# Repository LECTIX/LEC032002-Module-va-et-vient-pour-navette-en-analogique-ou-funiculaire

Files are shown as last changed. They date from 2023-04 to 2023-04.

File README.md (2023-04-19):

# LEC032002 - Module va et vient pour navette en analogique ou funiculaire
Fichiers sources pour le produit LEC032002

## Description du produit

- **AUTOMATIQUE** gérez votre train en mode navette ou votre funiculaire automatiquement
- **ACCÉLÉRATION** et freinage progressifs
- **TEMPORISATION** réglable entre 1 s et plus de 3 min
- **SIMPLICITÉ** Réglage facile de la vitesse maximum, du temps d'arrêt, de la courbe d'accélération et de freinage
- **SÉCURITÉ** Protection contre les courts circuits

## Utiliser les fichiers sources pour fabriquer le produit

Il n'est **pas nécessaire de savoir souder ou d'être bon en électronique** pour se procurer ce produit. Grâce aux fichiers sources publiés ici, vous pouvez être en mesure de faire fabriquer ce produit par un sous traitant.

**ATTENTION** ce produit nécessite une programmation afin de pouvoir fonctionner. Vous devez pour cela posséder le programmateur et programmer vous même la carte. Cette étape peut nécessiter des connaissances techniques, si nécessaire, nous vous encourrageons à vous rapprocher d'un club.

### Faire fabriquer chez un sous traitant

Il est aujourd'hui possible de faire fabriquer à moindre cout des cartes électroniques. Nous recommendons [JLCPCB](https://jlcpcb.com/) si vous voulez aller au moins cher. Si vous préférez un acteur européen, [eurocircuits](https://www.eurocircuits.com/) est un des acteurs reconnus.

IMAGE ALT TEXT (http://www.youtube.com/watch?v=RXGGvsUtz0c "TUTO : faire fabriquer un produit LECTIX")

1. Télécherger les sources de ce produit en cliquant sur le bouton `Code`, puis `Download ZIP`.
1. Décompresser le dossier.
1. Les fichiers pour la fabrication se trouvent dans le répertoire `hardware/prod`.
1. Se connecter sur [https://cart.jlcpcb.com/quote](https://cart.jlcpcb.com/quote)
1. Cliquer sur le bouton `Add gerber file` et sélectionner le fichier `gerbers.zip`.
1. Sélectionnez la quantité de cartes que vous souhaitez dans le champs `PCB Qty`.
1. Laisser toutes les autres options par défaut, puis cliquez sur le toggle switch en face de `PCB Assembly`, et enfin sur le bouton `confirm`.
1. Une preview de la carte électronique sans les composants doit apparaitre. Cliquez sur `NEXT`.
1. Cliquez sur le bouton `Add BOM File`, puis sélectionnez le fichier `bom.csv`
1. Cliquez sur le bouton `Add CPL File`, puis sélectionnez le fichier `pos.csv`
1. **Vérifier que tous les composants sont en stock** et bien sélectionnés, puis cliquez sur `NEXT`.
1. Une preview de la carte avec ses composants apparait. Continuer le chemin en cliquant sur `NEXT`.
1. Le prix final apparait. Sélectionnez la catégorie du produit, puis cliquez sur `SAVE TO CART`.
1. Une fois sauvegardé dans votre panier, vous pouvez valider votre commande et choisir le moyen d'acheminement. Afin de ne pas avoir à se préoccuper des frais de douane, nous vous conseillons de choisir une méthode d'expédition DDP.

Vous receverez vos cartes sous 1 à 3 semaines. 

**Nous ne sommes en aucun cas responsables des cartes qui arriveraient défectueuses ou non fonctionnelles.**

### Modifications des fichiers sources

Installez kicad 6 (ou version supérieure), et ouvrez le fichier LEC032002.kicad_pro

### Programation

Pour programmer le module, vous devez posséder
- un programmateur AVR type USBASP
- une sonde Tag-Connect TC2050

Le firmware se trouve dans le dossier du même nom. Il est recommandé d'utiliser VS-code et platform-io pour programmer la carte. Pour ce faire, branchez le programmateur à votre PC et à la carte à programmer, puis rentrer les commandes suivantes :

```
cd firmware
platformio run --target fuses && platformio run --target upload
```

### Regénérer les fichiers gerber, BOM, et position (Optionnel)

Peut se faire simplement en utilisant kikit :

```
cd hardware
docker run --rm -w /kikit -v $PWD:/kikit yaqwsx/kikit kikit fab jlcpcb --assembly --no-drc --schematic LEC032002.kicad_sch --field LCSC --corrections JLCPCB_CORRECTION --nametemplate LEC032002_{} LEC032002.kicad_pcb prod/

```
## Notices
[Manuel FR](docs/manual_fr.pdf)

## License
Tous nos fichiers sont plubliés sous les licenses
- CERN Open Hardware Licence Version 2 - Strongly Reciprocal pour ce qui touche au hardware
- GNU General Public License v3.0 pour tout ce qui est software

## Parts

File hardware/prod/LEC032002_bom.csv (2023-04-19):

Comment | Designator | Footprint | LCSC
100nF | C1,C3,C5,C7,C8,C9 | Capacitor_SMD:C_0603_1608Metric | C14663
100uF | C2,C6 | Capacitor_SMD:CP_Elec_6.3x7.7 | C249982
MB10S | D1 | Package_TO_SOT_SMD:TO-269AA | C2488
LED_green | D2 | LED_SMD:LED_0603_1608Metric | C72043
M7 | D3,D4,D5,D6,D7,D8,D9,D10 | Diode_SMD:D_SMA | C95872
LED_red | D11 | LED_SMD:LED_0603_1608Metric | C2286
Screw_Terminal_01x02_green | J1 | 0_connectors:TerminalBlock_bornier-2_P5.08mm-green | C395849
Screw_Terminal_01x02_blue | J2,J3,J4,J5 | 0_connectors:TerminalBlock_bornier-2_P5.08mm-blue | C430621
10k | R1,R2,R3,R9 | Resistor_SMD:R_0603_1608Metric | C25804
27R | R4,R5 | Resistor_SMD:R_0603_1608Metric | C25190
100k | R6,R7 | Resistor_SMD:R_0603_1608Metric | C25803
pot_smd_100k_3362P | RV1,RV2,RV3,RV4 | 0_potentiometers:BOURNS-3362P_pot | C118966
ATtiny24A-SSU | U1 | Package_SO:SOIC-14_3.9x8.7mm_P1.27mm | C14909
78L05G-AB3-R | U2 | Package_TO_SOT_SMD:SOT-89-3 | C71136
MP6515 | U3 | Package_SO:HTSSOP-16-1EP_4.4x5mm_P0.65mm_EP3.4x5mm_Mask3x3mm_ThermalVias | C114139
LTV-814S-TA1 | U4,U5 | Package_DIP:SMDIP-4_W9.53mm_Clearance8mm | C125118

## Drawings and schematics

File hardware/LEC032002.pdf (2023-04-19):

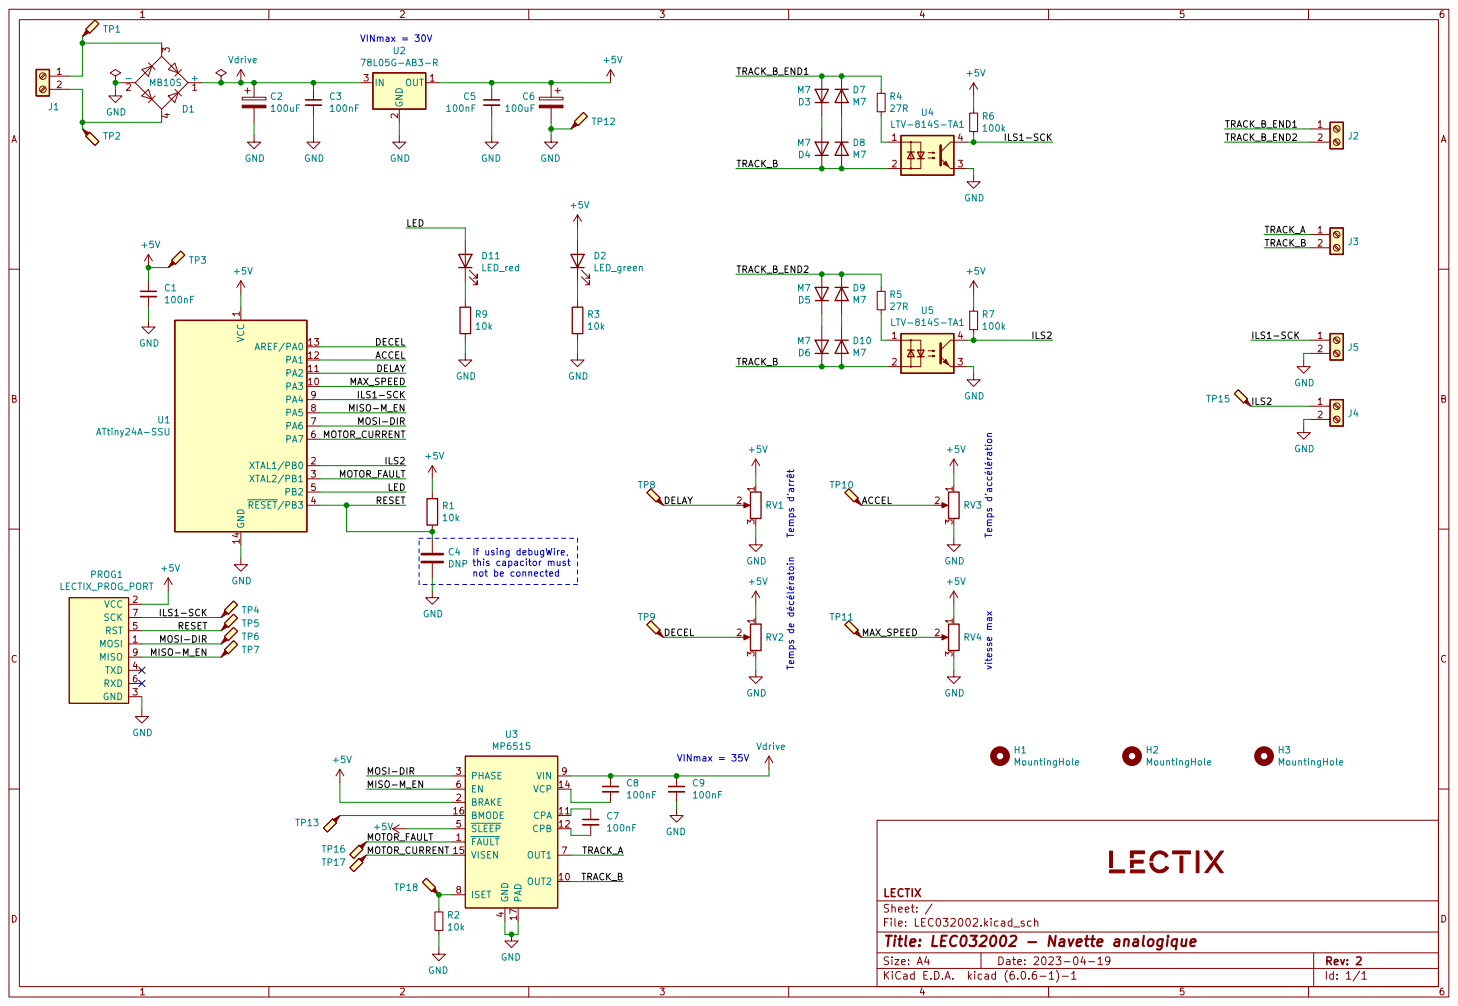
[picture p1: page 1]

1 PA3 10 PA2 11 PA1 12 AREF/PA0 13 GND 14 XTAL1/PB0 2 XTAL2/PB1 3 ~{RESET}/PB3 4 PB2 5 PA7 6 PA6 7 PA5 8 PA4 9 U1 ATtiny24A-SSU GND MOSI 1 VCC 2 GND 3 TXD 4 RST 5 RXD 6 SCK 7 MISO 9 PROG1

TRACK_A MISO-M_EN MOSI-DIR MISO-M_EN

Id: 1/1 Title: LEC032002 - Navette analogique

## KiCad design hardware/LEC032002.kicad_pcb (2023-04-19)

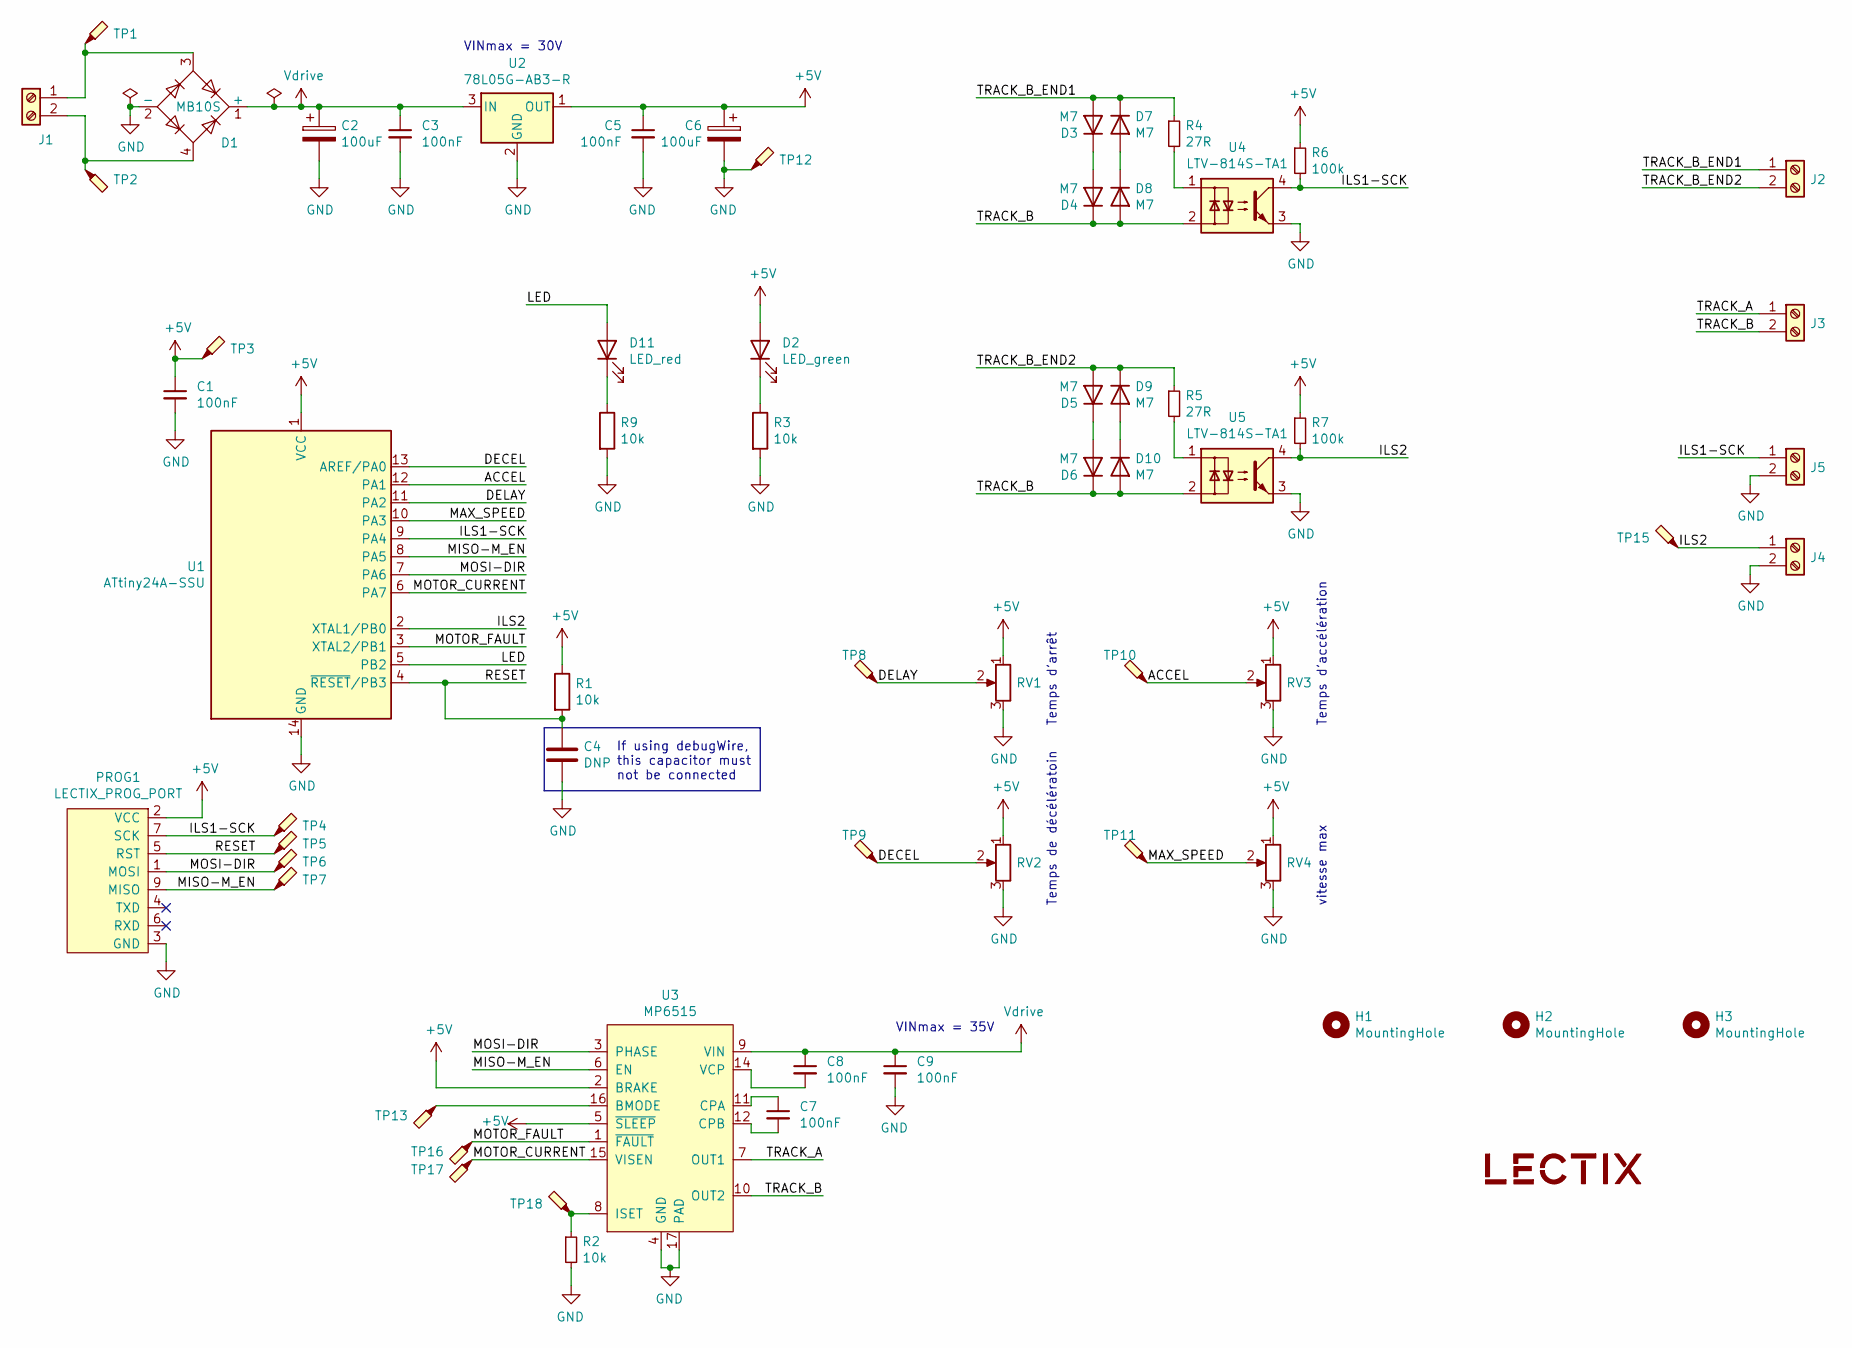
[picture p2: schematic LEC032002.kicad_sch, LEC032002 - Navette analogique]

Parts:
C1, C3, C5, C7, C8, C9: 100nF; C_0603_1608Metric; LCSC C14663
C2, C6: 100uF; CP_Elec_6.3x7.7; LCSC C249982
C4: DNP; C_0603_1608Metric; LCSC DNP
D1: MB10S; TO-269AA; LCSC C2488
D2: LED_green; LED_0603_1608Metric; MPN 19-217/GHC-YR1S2/3T; LCSC C72043
D3, D4, D5, D6, D7, D8, D9, D10: M7; D_SMA; MPN M7; LCSC C95872
D11: LED_red; LED_0603_1608Metric; LCSC C2286
H1, H2, H3: MountingHole; MountingHole_3.2mm_M3; LCSC DNP
J1: Screw_Terminal_01x02_green; TerminalBlock_bornier-2_P5.08mm-green; MPN DB126V-5.0-2P-GN; LCSC C395849
J2, J3, J4, J5: Screw_Terminal_01x02_blue; TerminalBlock_bornier-2_P5.08mm-blue; MPN DB301V-5.0-2P-BU-P; LCSC C430621
LOGO1: logo_lectix_25mm; Logo_10mm; LCSC DNP
PROG1: LECTIX_PROG_PORT; Tag-Connect_TC2050-IDC-FP_2x05_P1.27mm_Vertical; LCSC DNP
R1, R2, R3, R9: 10k; R_0603_1608Metric; LCSC C25804
R4, R5: 27R; R_0603_1608Metric; LCSC C25190
R6, R7: 100k; R_0603_1608Metric; LCSC C25803
RV1, RV2, RV3, RV4: pot_smd_100k_3362P; BOURNS-3362P_pot; MPN 3362P-1-104; LCSC C118966
TP1, TP2, TP3, TP4, TP5, TP6, TP7, TP8, TP9, TP10, TP11, TP12, TP13, TP15, TP16, TP17, TP18: TestPoint_Probe; TestPoint_Pad_D1.0mm; LCSC DNP
U1: ATtiny24A-SSU; SOIC-14_3.9x8.7mm_P1.27mm; LCSC C14909
U2: 78L05G-AB3-R; SOT-89-3; MPN 78L05G-AB3-R; LCSC C71136
U3: MP6515; HTSSOP-16-1EP_4.4x5mm_P0.65mm_EP3.4x5mm_Mask3x3mm_ThermalVi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; MPN MP6515GF-Z; LCSC C114139
U4, U5: LTV-814S-TA1; SMDIP-4_W9.53mm_Clearance8mm; MPN LTV-814S-TA1; LCSC C125118

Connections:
+5V: C1.1, C5.1, C6.1, D2.2 (A), PROG1.2 (VCC), R1.1, R6.1, R7.1, RV1.1, RV2.1, RV3.1, RV4.1, TP3.1, U1.1 (VCC), U2.1 (OUT), U3.2 (BRAKE), U3.5 (~SLEEP)
/ACCEL: RV3.2, TP10.1, U1.12 (PA1)
/DECEL: RV2.2, TP9.1, U1.13 (AREF/PA0)
/DELAY: RV1.2, TP8.1, U1.11 (PA2)
/ILS1-SCK: J5.1, PROG1.7 (SCK), R6.2, TP4.1, U1.9 (PA4), U4.4
/ILS2: J4.1, R7.2, TP15.1, U1.2 (XTAL1/PB0), U5.4
/LED: D11.2 (A), U1.5 (PB2)
/MAX_SPEED: RV4.2, TP11.1, U1.10 (PA3)
/MISO-M_EN: PROG1.9 (MISO), TP7.1, U1.8 (PA5), U3.6 (EN)
/MOSI-DIR: PROG1.1 (MOSI), TP6.1, U1.7 (PA6), U3.3 (PHASE)
/MOTOR_CURRENT: TP17.1, U1.6 (PA7), U3.15 (VISEN)
/MOTOR_FAULT: TP16.1, U1.3 (XTAL2/PB1), U3.1 (~FAULT)
/RESET: C4.1, PROG1.5 (RST), R1.2, TP5.1, U1.4 (~RESET/PB3)
/TRACK_A: J3.1, U3.7 (OUT1)
/TRACK_B: D4.1 (K), D6.1 (K), D8.2 (A), D10.2 (A), J3.2, U3.10 (OUT2), U4.2, U5.2
/TRACK_B_END1: D3.2 (A), D7.1 (K), J2.1, R4.1
/TRACK_B_END2: D5.2 (A), D9.1 (K), J2.2, R5.1
GND: C1.2, C2.2, C3.2, C4.2, C5.2, C6.2, C9.2, D1.2 (-), J4.2, J5.2, PROG1.3 (GND), PROG1.8 (GND), PROG1.10 (GND), R2.2, R3.2, R9.2, RV1.3, RV2.3, RV3.3, RV4.3, TP12.1, U1.14 (GND), U2.2 (GND), U3.4 (GND), U3.13 (GND), U3.17 (PAD), U4.3, U5.3
unnamed: C7.1, U3.11 (CPA)
unnamed: C7.2, U3.12 (CPB)
unnamed: C8.2, U3.14 (VCP)
unnamed: D1.3, J1.1, TP1.1
unnamed: D1.4, J1.2, TP2.1
unnamed: D2.1 (K), R3.1
unnamed: D3.1 (K), D4.2 (A)
unnamed: D5.1 (K), D6.2 (A)
unnamed: D7.2 (A), D8.1 (K)
unnamed: D9.2 (A), D10.1 (K)
unnamed: D11.1 (K), R9.1
unnamed: R2.1, TP18.1, U3.8 (ISET)
unnamed: R4.2, U4.1
unnamed: R5.2, U5.1
unnamed: TP13.1, U3.16 (BMODE)
Vdrive: C2.1, C3.1, C8.1, C9.1, D1.1 (+), U2.3 (IN), U3.9 (VIN)

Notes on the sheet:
VINmax = 35V
vitesse max
VINmax = 30V
Temps d’arrêt
If using debugWire, this capacitor must not be connected
Temps d’accélération
Temps de décélératoin

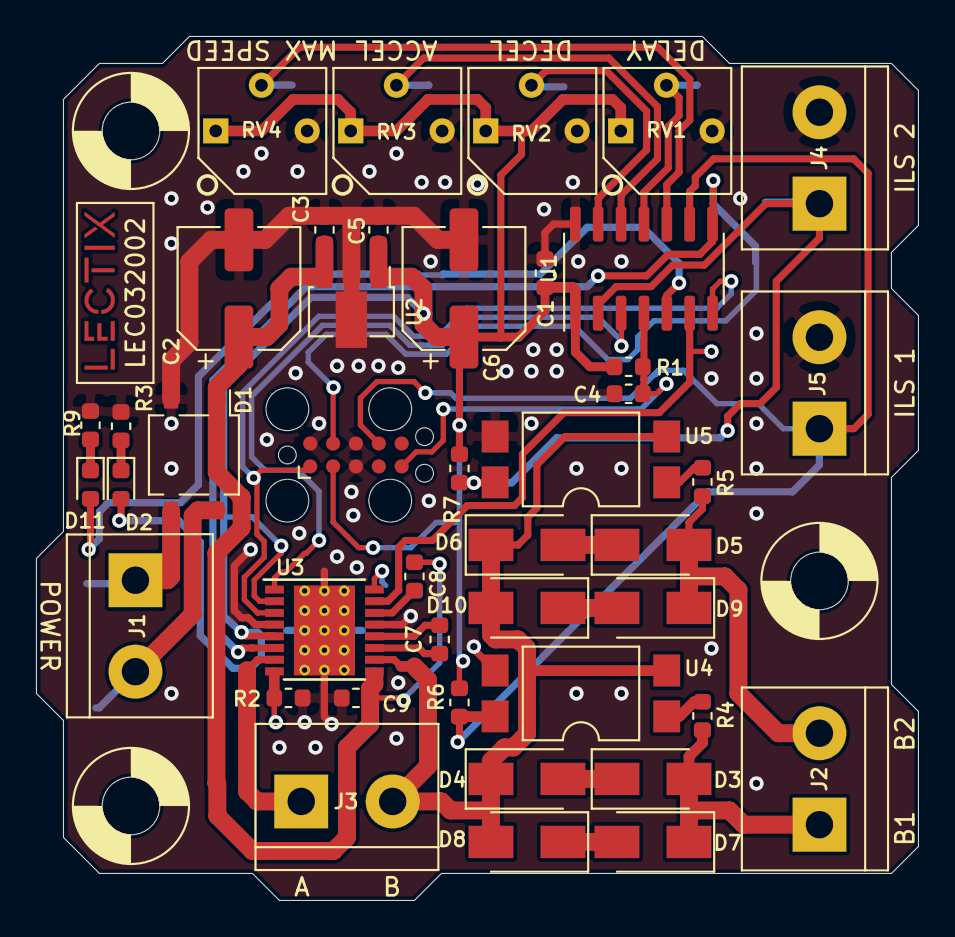
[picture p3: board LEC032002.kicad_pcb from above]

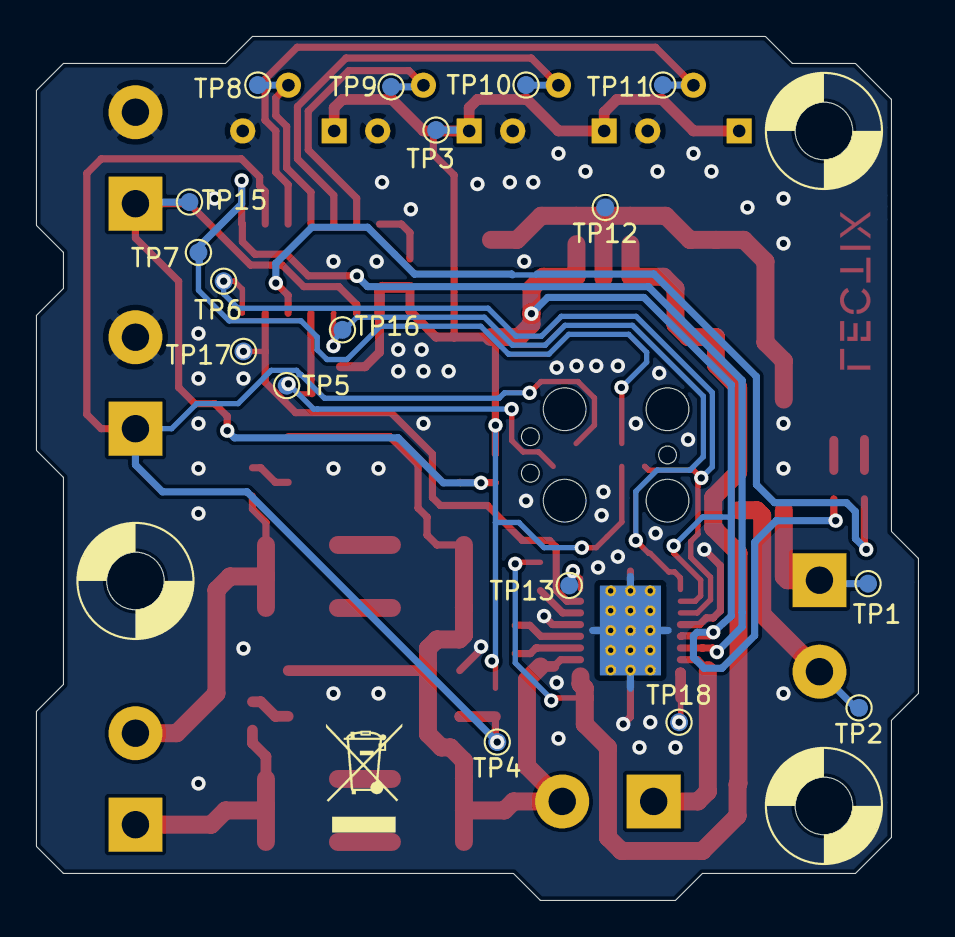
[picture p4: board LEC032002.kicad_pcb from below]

Board: 2 copper layers, 49.0 x 48.0 mm, 64 parts (17 on the bottom side), 34 nets.

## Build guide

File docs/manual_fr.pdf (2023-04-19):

# Module va et vient analogique

### LEC032002

☞ Avertissement : ce module n’est pas compatible avec les locomotives possédant un décodeur DCC (digital)!

## 1 Caractéristiques

- Mode navee (va et vient) automatique

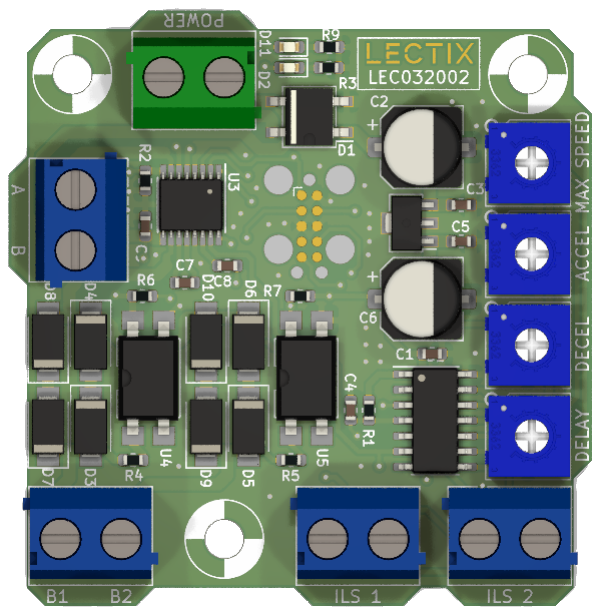
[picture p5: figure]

- Freinage et accélération progressive
- Détection des extrémités par analyse de la consommation de courant ou par capteurs ILS, pédales, ...
- Temporisation réglable entre 1 s et plus de 3 min
- Alimentation : 8 - 16 V DC
- Réglage facile de la vitesse maximum, du temps d’arrêt, de la courbe d’accélération et de freinage.
- Protection contre les courts circuits.
- 3 trous de fixation pour un montage facile.

## 2 Applications

- Mode navee (va et vient) automatique
- Mode navee (va et vient) via des capteurs de type ILS, pédale, ou équivalent
- Contrôle d’un funiculaire, ou de tout autre système motorisé DC

## 3 Specifications technique

Specification | Valeur | Unité
Temporisation avant redémarrage | 1 - 200 | sec
Tension d’alimentation | 8 - 16 | V DC
Intensité d’alimentation minimum recommandé | 1 | A
Intensité maximum en sortie du module | 1 | A

Table 1: Spécifications

LEC032002 - Module va et vient analogique rev 1.0.2 | 1

## 4 Utilisation

Le module va et vient analogique LEC032002 permet de créer facilement un mode navee automatisé pour votre réseau analogique. Il est également conçu pour piloter tout système à moteur DC devant changer de sens à intervalle régulier. On note notamment parmi ces systèmes le pilotage d’un funiculaire à l’aide d’un moteur et de 2 ILS.

L’installation du module est facile, le réglage des paramètres (vitesse maximum, temporisation avant redémarrage, accélération, freinage) se fait simplement en tournant les potentiomètres à l’aide d’un tournevis.

### 4.1 Installation et câblage du module pour un va et vient automatique

Le module doit être câblé tel que sur la figure 3.

1. Connecter une alimentation entre 8 et 16 V DC au bornier d’alimentation. Cee alimentation sera indirectement reliée à la voie, il faut donc que la tension d’alimentation soit compatible avec la tension d’utilisation de vos trains.
2. Connecter la voie sur le bornier de sortie (bornier "A B").
3. Connecter au choix :
- [Détection par consommation de courant] les rails droits isolés sur les 2 zones d’arrêt aux borniers B1 et B2 (Cf. Figure 1).
- [Détection par ILS, pédale, ...] les 2 ILS marquant le début des zones d’arrêt sur les borniers ILS1 et ILS2 (Cf. Figure 2).

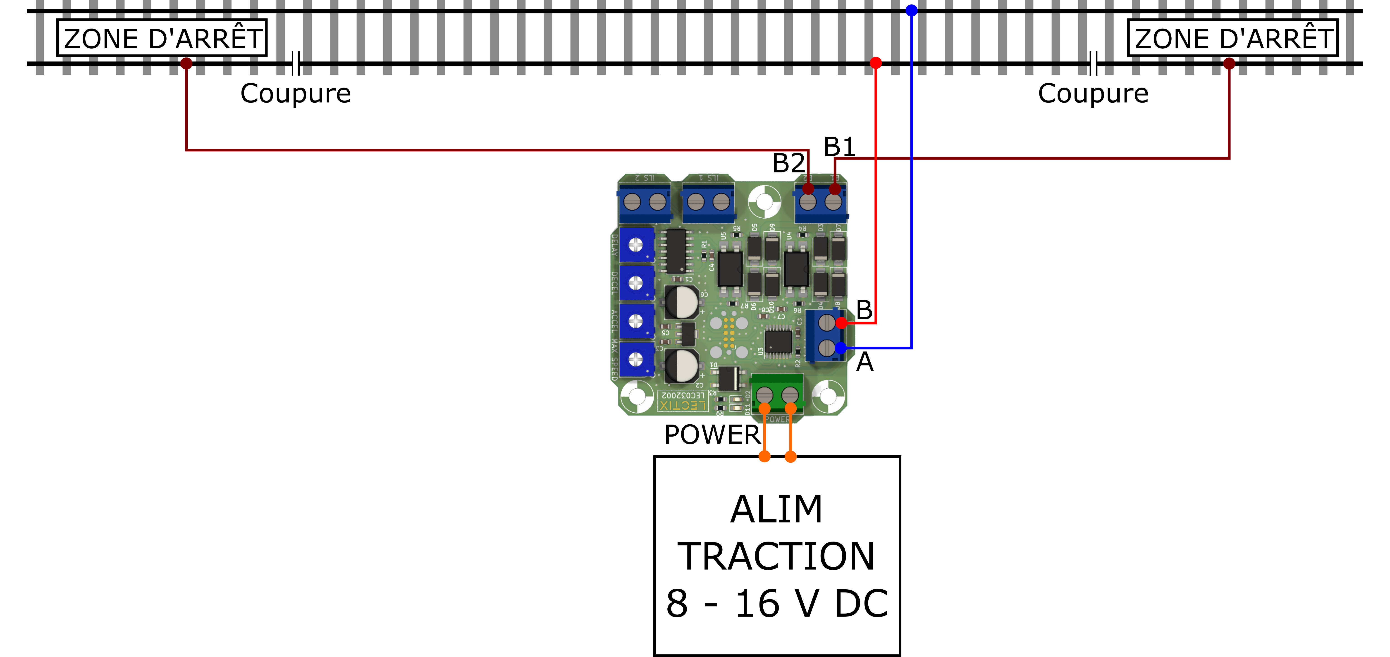
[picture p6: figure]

Figure 1: Schéma de câblage du module pour un va et vient analogique avec détection des zones de freinages par analyse de la consommation de courant.

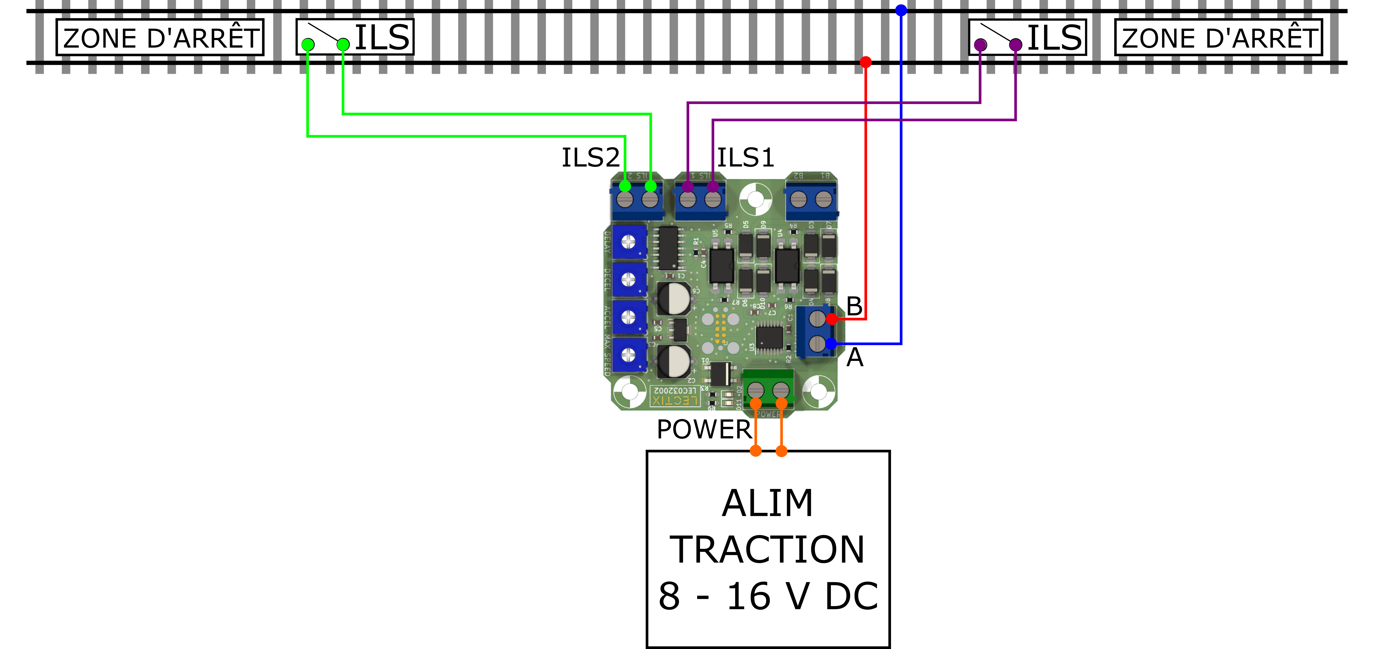
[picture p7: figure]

Figure 2: Schéma de câblage du module pour un va et vient analogique avec détection des zones de freinage par ILS (ou capteurs équivalents).

Une fois le module installé, il faut s’assurer que

- les ILS, capteurs de consommation (ou capteurs équivalents) soient bien branchés par rapport au sens de fonctionnement du train.
- le temps de freinage ne soit pas trop important, pour ne pas provoquer de collisions.

Pour ce faire, suivez les étapes suivantes :

1. mere le train au milieu de la voie (en dehors des zones de freinage donc)
2. tournez le potentiomètre du temps de décélération (DECEL) à fond dans le sens des aiguilles d’une montre. Cela aura pour eet d’arrêter immédiatement le train lorsqu’il rentrera dans la zone d’arrêt.
3. allumez le module en branchant son alimentation.

Si les capteurs sont branchés sur les bons borniers, le train doit s’arrêter immédiatement dès lors qu’il rentre dans la zone d’arrêt. Si le train continue au delà du capteur utilisé pour marquer le début de la zone de freinage, arrêtez immédiatement le module et inversez le branchement des capteurs (branchez les fils auparavant sur le bornier "ILS1" sur le bornier "ILS2", et inversement, ou respectivement "B1" et "B2" si utilisation des capteurs de consommation de courant).

Recommencez l’opération pour s’assurer que le fonctionnement est à présent correct, puis Rendez vous section suivante pour ainer le réglage du module.

### 4.2 Installation et câblage du module pour animer un funiculaire

1. Connecter une alimentation entre 8 et 16 V DC au bornier d’alimentation. Cee alimentation sera indirectement reliée à la voie, il faut donc que la tension d’alimentation soit compatible avec la tension d’utilisation du moteur.
2. Connecter le moteur sur le bornier de sortie (bornier "A B").
3. Connecter les 2 ILS sur les borniers ILS1 et ILS2.

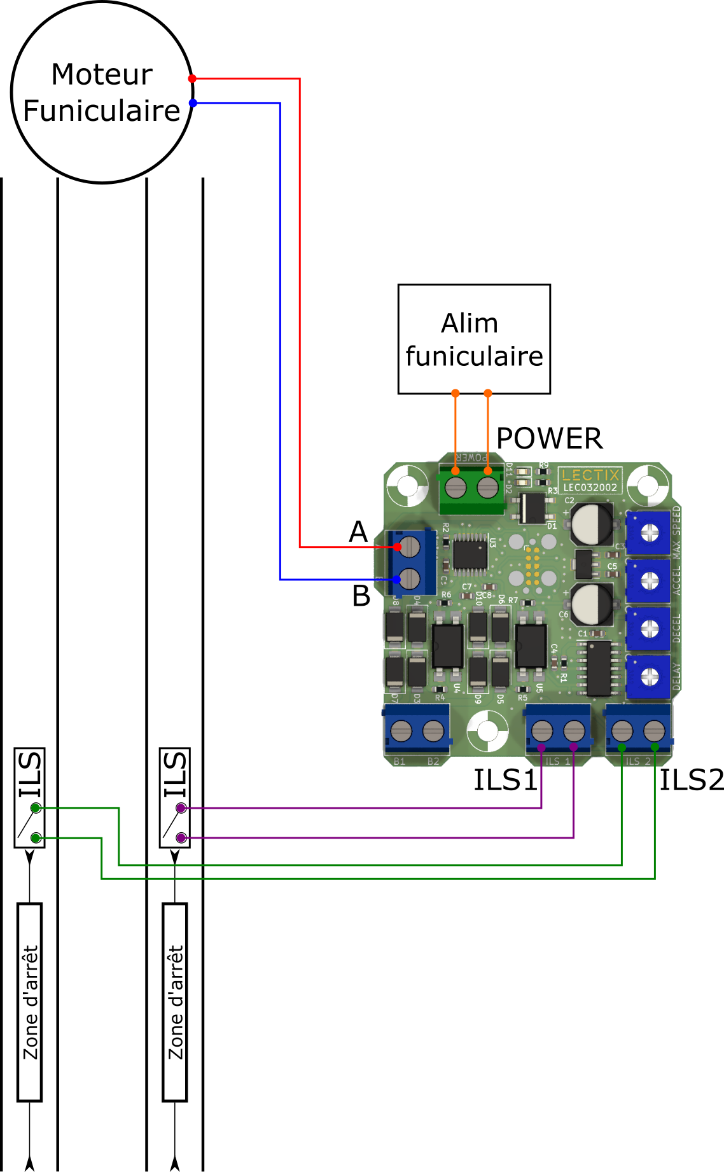
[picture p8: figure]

Figure 3: Schéma de câblage du module pour piloter un funiculaire.

Une fois le module installé, il faut s’assurer que

- les ILS (ou capteurs équivalents) soient bien branchés par rapport au sens de fonctionnement du moteur.
- le temps de freinage ne soit pas trop important, pour ne pas provoquer de collisions.

Pour ce faire, suivez les étapes suivantes :

1. mere le funiculaire au milieu des voies (en dehors des zones de freinage donc)
2. tournez le potentiomètre du temps de décélération (DECEL) à fond dans le sens des aiguilles d’une montre. Cela aura pour eet d’arrêter immédiatement le funiculaire lorsqu’il rentrera dans la zone d’arrêt.
3. allumez le module en branchant son alimentation.

Si les ILS sont branchés sur les bons borniers, le funiculaire doit s’arrêter immédiatement dès lors qu’il rentre dans la zone d’arrêt. Si le funiculaire continue au delà du capteur utilisé pour marquer le début de la zone de freinage, arrêtez immédiatement le module et inversez les 2 ILS (branchez les fils auparavant sur le bornier "ILS1" sur le bornier "ILS2", et inversement).

Recommencez l’opération pour s’assurer que le fonctionnement est à présent correct.

### 4.3 Réglage des paramètres

Cee section décrit une méthode pour régler les paramètres du module, à savoir vitesse maximum, temporisation avant redémarrage, temps d’accélération et de décélération. Il est conseillé d’utiliser un petit tournevis plat pour régler les potentiomètres.

☞ Note : Aention à ne pas forcer si le potentiomètre bloque, sous risque de détéri-

oration.

1. Pour commencer, régler tous les paramètres de la façon suivante :
- vitesse max ("MAX SPEED") => tourner le potentiomètre à fond dans le sens des aiguilles d’une montre.
- temporisation avant redémarrage ("DELAY") => tourner le potentiomètre à fond dans le sens inverse des aiguilles d’une montre.
- temps d’accélération ("ACCEL") => tourner le potentiomètre à fond dans le sens des aiguilles d’une montre.
- temps de décélération ("DECEL") => tourner le potentiomètre à fond dans le sens des aiguilles d’une montre.
2. Mere en route le module, et s’assurer que le va et vient fonctionne.
3. Régler la vitesse maximale qui vous convient le mieux en tournant, si nécessaire, le potentiomètre "MAX SPEED".
4. Régler le temps de décélération en tournant le potentiomètre ’DECEL’.
5. Régler le temps d’accélération en tournant le potentiomètre ’ACCEL’.
6. Enfin, régler la temporisation avant redémarrage en ajustant le potentiomètre "DELAY".

## 5 Dimensions

Le module dispose de 3 trous de fixation permeant de faire passer des vis de 3 mm.

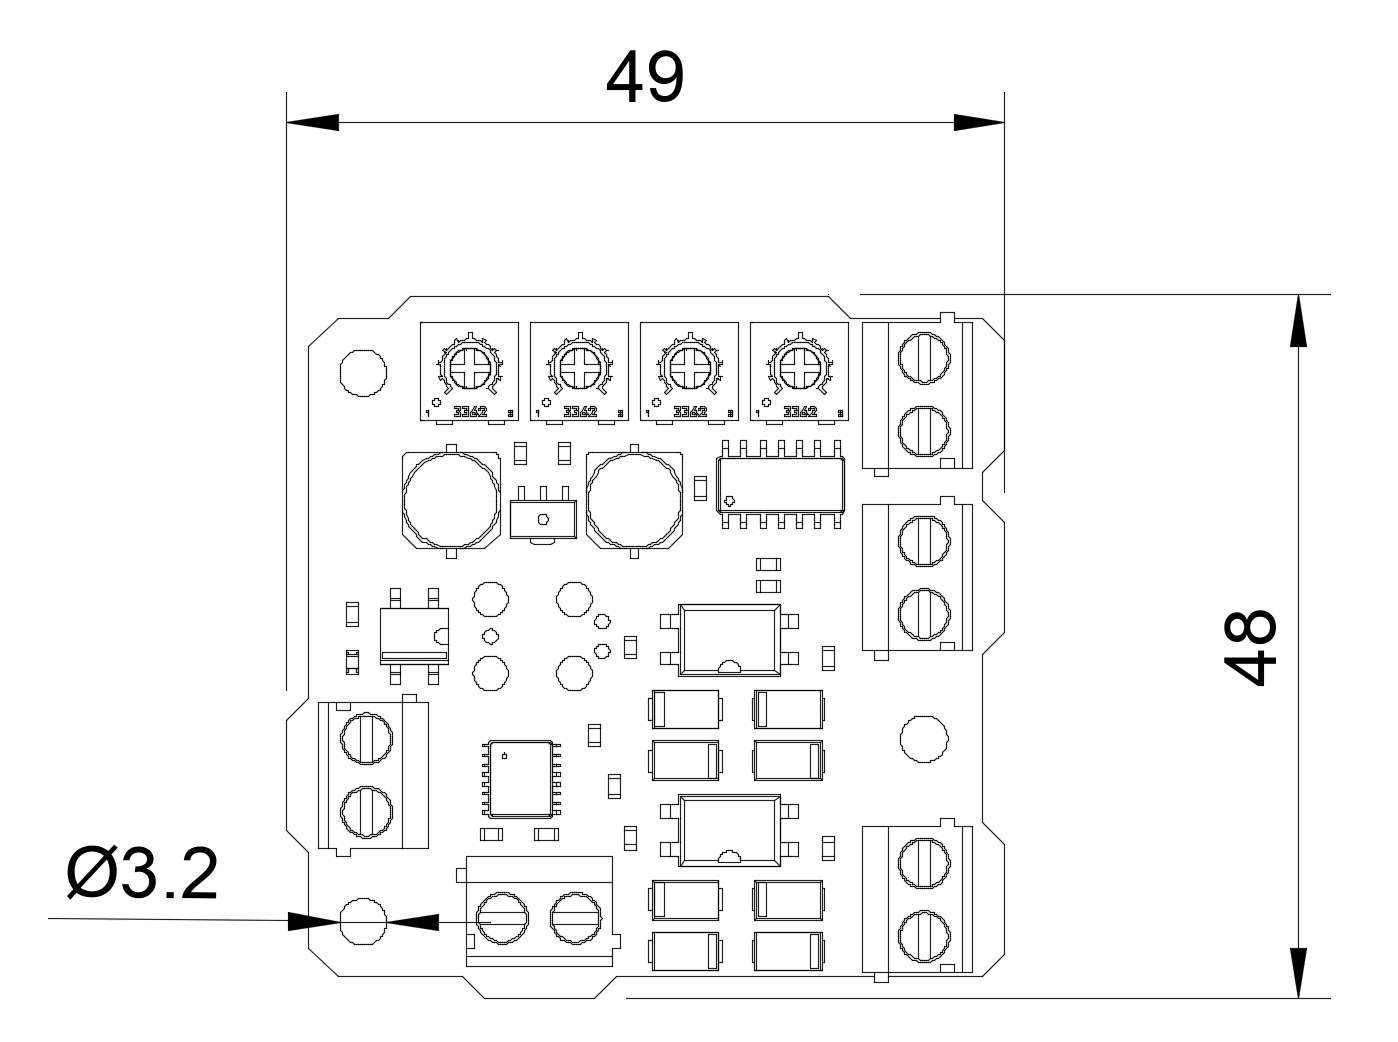
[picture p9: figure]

Figure 4: Dimensions du module (toutes les côtes sont données en mm).

## 6 Contact et SAV

Pour tout renseignement, veuillez vous adresser à contact@lectix.fr.

## 7 Revision History

Revision | Date | Author(s) | Description
1.0.0 | 26.12.21 | TFC | Création du document
1.0.1 | 30.12.21 | TFC | Ajout de la section câblage va et vient
1.0.2 | 20.04.22 | TFC | Mise à jour de version du module

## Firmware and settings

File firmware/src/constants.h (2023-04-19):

#ifndef CONSTANTS_H
#define CONSTANTS_H

/**
 * PB0  0       PCINT8  XTAL1
 * PB1  1       PCINT9  XTAL2
 * PB3  11      PCINT11 RESET
 * PB2  2       PCINT10 OC0A    INT0
 * PA7  3   A7  PCINT7  OC0B
 * PA6  4   A6  PCINT6  MOSI    DI  SDA OC1A
 * PA5  5   A5  PCINT5  MISO    DO  OC1B
 * PA4  6   A4  PCINT4  SCK     SCL 
 * PA3  7   A3  PCINT3
 * PA2  8   A2  PCINT2  AIN1
 * PA1  9   A1  PCINT1  AIN0
 * PA0  10  A0  PCINT0  AREF
 */ 


#define PIN_DECEL A0
#define PIN_ACCEL A1
#define PIN_DELAY A2
#define PIN_MAX_SPEED A3
#define PIN_ILS1 6
#define PIN_MOTOR_EN 5
#define PIN_MOTOR_DIR 4
#define PIN_MOTOR_CURRENT A7
#define PIN_ILS2 0
#define PIN_MOTOR_FAULT 1
#define PIN_LED 2

// Constants

#define DEFAULT_ACCELERATION 5
#define DEFAULT_DECELERATION 5
#define DEFAULT_MAX_SPEED 255
#define MIN_MAXIMUM_SPEED 50

#define FORWARD_DIR 0
#define BACKWARD_DIR 1

#endif

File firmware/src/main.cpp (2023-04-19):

#include <Arduino.h>
#include "constants.h"
#include "MP6515.h"
#include <EEPROM.h>

uint32_t lastTriggerTmstp = 0;
uint32_t pauseStartTime = 0;
uint32_t pauseDuration = 0;
uint8_t direction = FORWARD_DIR;
uint8_t stateAddr = 1;

enum STATE
{
    INIT,
    WAITING_FOR_STOP_TRIGGER,
    BREAKING,
    PAUSE
};

static STATE state = INIT;

void updateMotorSettings()
{
    motor.setAcceleration(analogRead(PIN_ACCEL) << 4);
    motor.setDeceleration(analogRead(PIN_DECEL) << 4);
    motor.setMaxSpeed(255 - ((analogRead(PIN_MAX_SPEED) >> 2) & 0x00FF));
    pauseDuration = 200ULL * (1024 - analogRead(PIN_DELAY));
}

void registerDir(uint8_t dir)
{
    EEPROM.update(stateAddr, dir); // save next direction in case of shutdown
}

void setup()
{
    pinMode(PIN_MOTOR_EN, OUTPUT);
    pinMode(PIN_LED, OUTPUT);
    pinMode(PIN_MOTOR_DIR, OUTPUT);
    pinMode(PIN_MOTOR_FAULT, INPUT_PULLUP);
    pinMode(PIN_ILS1, INPUT);
    pinMode(PIN_ILS2, INPUT);

    updateMotorSettings();

    stateAddr = EEPROM.read(0);
    direction = EEPROM.read(stateAddr);
    stateAddr++;
    if (stateAddr == 0)
        stateAddr = 1;
    else if (stateAddr > 127)
        stateAddr = 1;
    EEPROM.write(0, stateAddr);
    registerDir(direction);

    motor.begin(direction);
}

void loop()
{
    digitalWrite(PIN_LED, !digitalRead(PIN_MOTOR_FAULT));
    motor.loop();
    if (millis() - lastTriggerTmstp > 100)
    {
        lastTriggerTmstp = millis();
        updateMotorSettings();
    }

    switch (state)
    {
    case INIT:
    {
        motor.move(direction);
        state = WAITING_FOR_STOP_TRIGGER;
        break;
    }

    case WAITING_FOR_STOP_TRIGGER:
    {
        uint8_t sensorPin = PIN_ILS2;
        if (direction == FORWARD_DIR)
            sensorPin = PIN_ILS1;

        if (digitalRead(sensorPin) == 0)
        {
            bool falseTrigger = false;
            lastTriggerTmstp = millis();
            while (millis() - lastTriggerTmstp < 10)
                falseTrigger |= digitalRead(sensorPin) == 1;
            if (falseTrigger == false)
            {
                registerDir(!direction); // save next direction in case of shutdown
                motor.brake();
                state = BREAKING;
            }
        }
        break;
    }

    case BREAKING:
    {
        if (motor.getSpeed() == 0)
        {
            pauseStartTime = millis();
            state = PAUSE;
            direction = !direction;
        }
        break;
    }

    case PAUSE:
    {
        if (millis() - pauseStartTime > pauseDuration)
        {
            state = INIT;
        }
        break;
    }

    default:
        break;
    }
}

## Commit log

2023-04-19 Add hardware source files
    [LEC032002-CmtUser.gbr, LEC032002-CuBottom.gbl, LEC032002-CuTop.gtl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]
2023-04-19 Fix part placement
    [LEC032002-CmtUser.gbr, LEC032002-CuBottom.gbl, LEC032002-CuTop.gtl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]
